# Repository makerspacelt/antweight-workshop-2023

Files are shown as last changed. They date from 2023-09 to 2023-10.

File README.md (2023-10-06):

#antweightKMS2023

DIY Cheap Antweight Robot Controlled with bluetooth mobile device using dabble app. (Lithuanian Antweight format - 200g)
NOTE - IOS doesn't support "analog" joystick, only "digital" buttons.
Total cost of everything (if you source 1cell lithium battery yourself) - around 15eur

https://vi.aliexpress.com/item/1005004255557549.html 1pair of wheels (sold by pair)

https://vi.aliexpress.com/item/4000083406292.html 1pcs motor driver

https://vi.aliexpress.com/item/1005004337178335.html 1vnt ESP32 (the cheaper ones work)

https://vi.aliexpress.com/item/1005004500537507.html 4pcs 26Awg red black (sold by 100pcs)

https://vi.aliexpress.com/item/33022320164.html 2vnt N20 motors 6v 300rpm

https://vi.aliexpress.com/item/1005004985397880.html 3pcs "top entry" jst xh connector (sold by 100pcs)

https://vi.aliexpress.com/item/1005005037876729.html 1pcs TP4056 charger

https://vi.aliexpress.com/item/32810326460.html 1pcs Boost module

https://vi.aliexpress.com/item/4000278469653.html 2pcs 15P and 2pcs 6P (sold by more pcs)

https://vi.aliexpress.com/item/33012530737.html 1vnt MTS103 switch (not the best, easy to turn off)

Plastic- ~80g one robot, recommendation - filalab.shop

Screws:
6mm round 4pcs (for mounting the pcb)
6mm flat 9pcs (countersunk) (for top panel and front panel mounting)
10mm flat 4pcs (countersunk) (for side panel mounting)
20mm flat 8pcs (countersunk) (for motor mounting

PCB 30pcs ~15eur
PCB has two input voltage connectors. You can use the second connector for connecting a second battery, internal charger or another device (for example - ESC). The pcb also has a LED thats connected to D23 and is programmable and also it has an expension port for servo or esc use. 

Batteries - you can use any 1s lithium battery, the 3d files have a slot for 18650 but for real fights it's too heavy. Another cheap option are vape batteries that prefferably are >400mAh. With 1 battery you can expect quite a long run time still. 
If you decide to use vape battery, then the weight of the robot will be ~190g if the plastic used is PLA or PETG. 

You can also use 2s batteries, but the total price would increase by ~5eur. The cheapest available 2s batteries are from Chinahobbyline. 





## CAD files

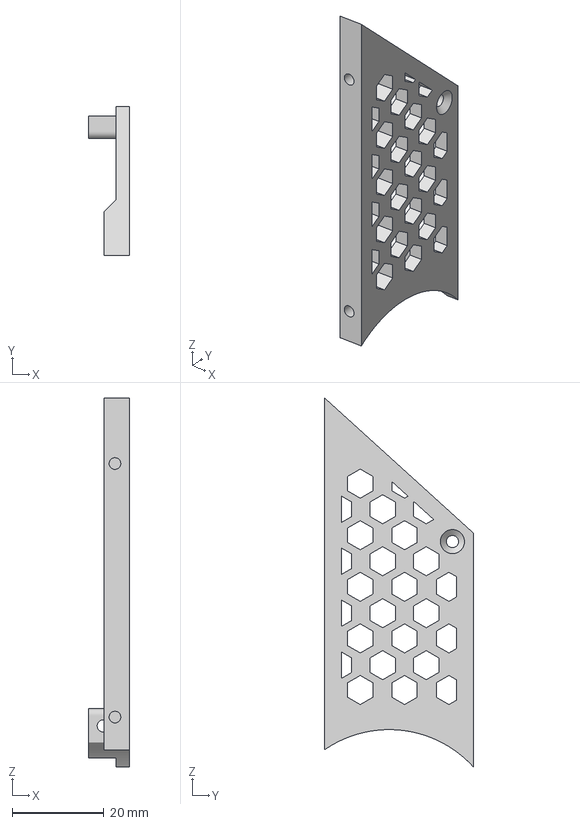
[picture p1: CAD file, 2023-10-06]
LeftWall.3mf
9.00 x 32.4 x 80.5 mm

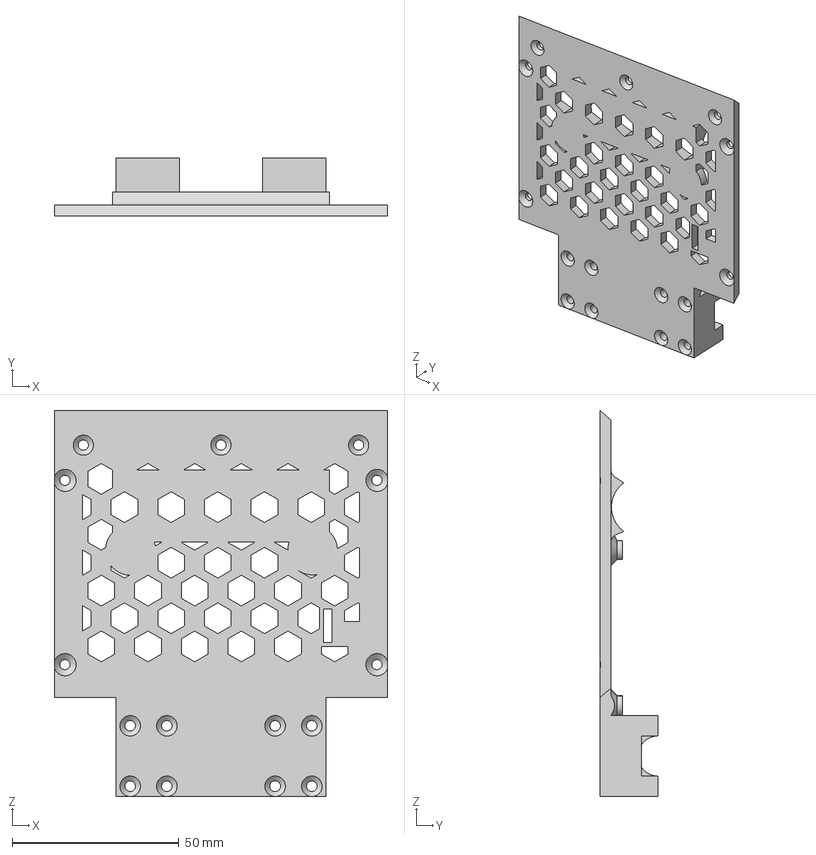
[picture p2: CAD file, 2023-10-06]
Bottom.3mf
100.0 x 17.3 x 115.8 mm

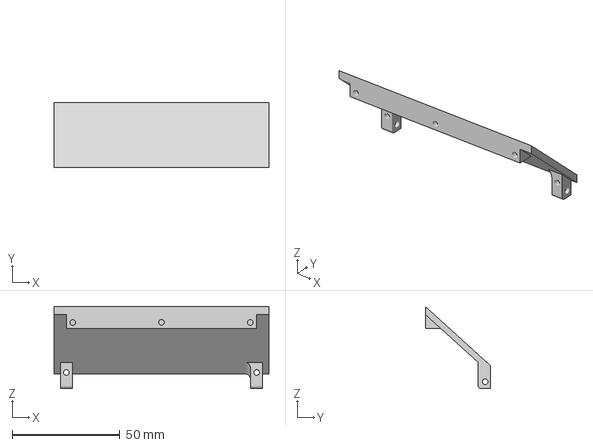
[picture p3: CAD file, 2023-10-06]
Front.3mf
100.0 x 30.4 x 38.2 mm

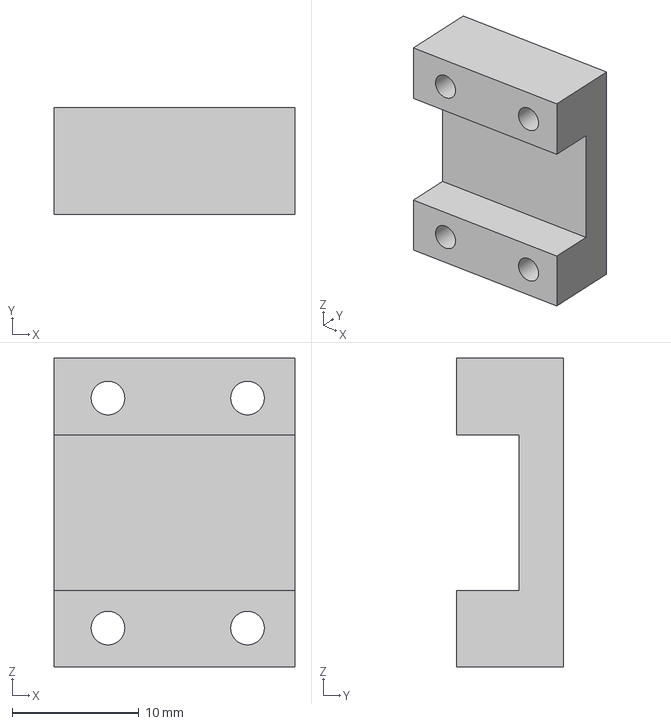
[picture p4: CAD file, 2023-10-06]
RightMotorMount.3mf
19.0 x 8.45 x 24.4 mm

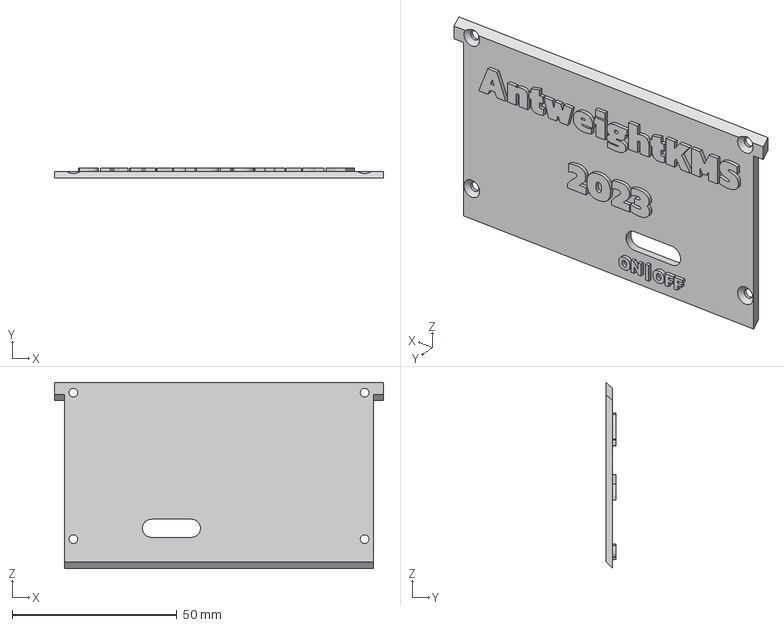
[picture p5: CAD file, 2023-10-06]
Top.3mf
100.0 x 3.00 x 56.6 mm

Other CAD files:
LeftMotorMount.3mf
RightWall.3mf

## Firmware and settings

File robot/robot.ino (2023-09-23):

/*
   Docs: https://thestempedia.com/docs/dabble/game-pad-module/
   Android app: https://play.google.com/store/apps/details?id=io.dabbleapp
   iOS app: https://apps.apple.com/us/app/dabble-bluetooth-controller/id1472734455?ls=1

   Arduino Libraries (install using Library Manager):
   * DabbleESP32
   * Cdrv8833
   Board (install ESP32 from espressif using Board Manager):
   * ESP32 Dev Module
*/

#define ROBOT_NAME "Zolinis stumbras"

#define CUSTOM_SETTINGS
#define INCLUDE_GAMEPAD_MODULE
#include <DabbleESP32.h>
#include "Cdrv8833.h"

// Uncomment this if the red motor wire is on the left
// when looking from the back of the motor.
#define M1_M2_PINS_INVERT 1

#ifndef M1_M2_PINS_INVERT
// M1 & M2 connected correctly (plus on PCB is red wire)
#define PIN_IN1 26
#define PIN_IN2 25
#define PIN_IN3 13
#define PIN_IN4 27
#else
// M1 & M2 connected incorrectly (plus on PCB is black wire)
#define PIN_IN1 25
#define PIN_IN2 26
#define PIN_IN3 27
#define PIN_IN4 13
#endif
#define CHANNEL 0 // PWM channel (0..15)
#define SWAP    false // swap motor rotation direction 

Cdrv8833 M1;
Cdrv8833 M2;

const float pi180 = 0.017453292519943295;
const float mag_min = 0.0;
const float mag_max = 6.0;
const float mag_scale = 1.0 / 6.0;
const float mag_scaled_start = 0.5;

float m1_spd_prev = 0.0;
float m2_spd_prev = 0.0;
float m1_spd = 0.0;
float m2_spd = 0.0;

float min_spd = -100.0;
float max_spd = 100.0;

unsigned long ms;

void setup() {
  // put your setup code here, to run once:
  Serial.begin(115200);      // make sure your Serial Monitor is also set at this baud rate.
  Dabble.begin(ROBOT_NAME);  // set bluetooth name of your device

  M1.init(PIN_IN1, PIN_IN2, CHANNEL, SWAP);
  M1.setDecayMode(drv8833DecayFast);
  M2.init(PIN_IN3, PIN_IN4, CHANNEL, SWAP);
  M2.setDecayMode(drv8833DecayFast);
}

void loop() {
  // Refresh data obtained from smartphone.
  Dabble.processInput();
  
  ms = millis();

  // The distance from the center of the joystick.
  // This value varies from 0 to 7. At the center, the value is 0 and on the perimeter of the joystick, the value is 7.
  float mag = GamePad.getRadius();

  // Angle between the positive x-axis and the line joining the center and the current position of the dot.
  // It varies from 0 to 360 at a step of 15 degrees.
  float a = GamePad.getAngle();

  if (mag > mag_max) mag = mag_max;
  mag = mag * mag_scale;
  if (mag > 0) {
    if (mag < mag_scaled_start) mag = mag_scaled_start;
  }

  float sina = sin(a * pi180);
  float cosa = cos(a * pi180);
  
  // calculate target speed
  m1_spd = mag * (sina - cosa) * max_spd;
  m2_spd = mag * (sina + cosa) * max_spd;

  // "Digital Mode" up/down/left/right buttons
  if (GamePad.isUpPressed()) {
    m1_spd = 100;
    m2_spd = 100;
  }
  else if (GamePad.isDownPressed()) {
    m1_spd = -100;
    m2_spd = -100;
  }
  else if (GamePad.isLeftPressed()) {
    m1_spd = 100;
    m2_spd = -100;
  }
  else if (GamePad.isRightPressed()) {
    m1_spd = -100;
    m2_spd = 100;
  }

  
  m1_spd = constrain(m1_spd, min_spd, max_spd);
  m2_spd = constrain(m2_spd, min_spd, max_spd);

  // motor needs a lot of start current to get running.
  // if it wasn't running previously, then kick it hard
  // (though one cycle is probably not enough).
  if (m1_spd_prev == 0.0) {
    if (m1_spd > 0) m1_spd = 100;
    else if (m1_spd < 0) m1_spd = -100;
  }
  if (m2_spd_prev == 0.0) {
    if (m2_spd > 0) m2_spd = 100;
    else if (m2_spd < 0) m2_spd = -100;
  }

  m1_spd_prev = m1_spd;
  m2_spd_prev = m2_spd;

  M1.move(m1_spd);
  M2.move(m2_spd);

  if (ms % 100 == 0) {
    Serial.print("mag=");
    Serial.print(mag);
    Serial.print(" a=");
    Serial.print(a);
    Serial.print(" m1=");
    Serial.print(m1_spd);
    Serial.print(" m2=");
    Serial.print(m2_spd);
    Serial.println();
  }

  // All modes - buttons
  //if (GamePad.isCrossPressed())
  //if (GamePad.isTrianglePressed())
  // if (GamePad.isCirclePressed())
  // if (GamePad.isSquarePressed())
  //if (GamePad.isStartPressed())
  //if (GamePad.isSelectPressed())
}

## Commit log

2023-09-23 fix pins for workshop bot
    [robot.ino]
2023-09-23 add option for different M1 & M2 wiring
2023-10-06 Adding 3D files, gerbers and instructions
    * Added .3mf files for 3d printing, also gerber.
    * Update README.md
    * Updated PCB Design with bug fix
    transfered vcc from error pin to EEP pin
    [Bottom.3mf, Front.3mf, LeftMotorMount.3mf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]
